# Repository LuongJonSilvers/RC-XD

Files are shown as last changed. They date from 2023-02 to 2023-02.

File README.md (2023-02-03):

# RC-XD
Capstone Project for Embedded Microprocessor System Design Course
Partners: Grant Smith, Sreenivas Krishna Nair, Valente Arroyo, & Akash Chinthamani
This is my capstone project for the final semester at the University Of Wisconsin Madison. This project uses C code with a Hardware abstraction layer(Cypress Cyhal) that is running on a PSoC6. The PSoC6 is a microprocessor that has many features. We were tasked with designing PCB(s), assemblying, coding, debugging, and testing our product. We used Altium Designer and Eclipse IDE for ModusToolbox for this project heavily. The project itself is a APP controlled car platform that can take on many hardware modules to change its funcitonality. This car platform comes with a live camera feed, GPS, crash detection, automatic headlights and a designated app for control. For our final demo we decided to equip the bot with a turret that shot water pellets. Originally this repo was on a partners account which I have transeferred here. The working files that live here include: Presentations/writeup reports, Altium Schematics and PCB docs, C code, python OPENCV code, and Kotlin code files. A project demo can be found following this link : https://www.youtube.com/watch?v=NHO1YES_Jxg&ab_channel=GrantSmith

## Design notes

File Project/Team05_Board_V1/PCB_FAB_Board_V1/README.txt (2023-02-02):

The board outline is defined by a 10mil trace defined on all gerbers.

The board dimensions are 7.2 x 5.8 inches.

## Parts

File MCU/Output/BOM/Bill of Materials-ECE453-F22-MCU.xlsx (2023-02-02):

Description | Designator | Footprint | Quantity | Supplier 1 | Supplier Part Number 1 | Supplier Stock 1
CAP CER 10UF 10V X5R 0805 | C200, C201 | FP-C0805C-DG-MFG | 2 | Digi-Key | 399-C0805C106K8PAC7800CT-ND
CAP CER 0.1UF 50V X7R 0805 | C202, C203 | FP-C0805C-DN-MFG | 2 | Digi-Key | 399-C0805C104K5RAC7800CT-ND
 | C204, C205 | CAPC2013X94X50LL20T25 | 2 | Digi-Key | 478-11894-1-ND
DIODE SCHOTTKY 40V 1A SMA | D200 | FP-SMA-MFG | 1 | Digi-Key | B140-FDICT-ND
SMD mono-color Chip LED, WL-SMCW, Red | LED200 | 0805_A | 1 | Digi-Key | 732-4984-1-ND
SMD mono-color Chip LED, WL-SMCW, Green | LED201 | 0805_A | 1 | Digi-Key | 732-4983-1-ND
RF TXRX MOD BLUETOOTH TRACE ANT | MD200 | FP-CYBLE-416045-02-MFG | 1 | Digi-Key | 428-4622-1-ND
THT Vertical Pin Header WR-PHD, Pitch 2.54 mm, Single Row, 5 pins | P200 | 61300511121 | 1 | Digi-Key | 732-5318-ND
Chip Resistor, 330 Ohm, +/- 1%, 125 mW, -55 to 155 degC, 0805 (2012 Metric), RoHS, Tape and Reel | R200, R202 | RESC2013X60X35LL10T20 | 2 | Digi-Key | 311-330CRCT-ND
Chip Resistor, 10 KOhm, +/- 1%, 0.125 W, -55 to 155 degC, 0805 (2012 Metric), RoHS, Tape and Reel | R201, R203, R204 | RESC2013X60X35NL10T20 | 3 | Digi-Key | 311-10.0KCRCT-ND
Swicth, SPST, 24 V, -35 to 85 degC, 4-Pin SMD, RoHS, Tape and Reel | SW200, SW201 | TECO-FSM4JSMA_V | 2 | Digi-Key | 450-1129-ND
Test Point, 1 Position SMD, RoHS, Tape and Reel | TP200, TP201, TP202, TP203 | KSTN-5019_V | 4 | Digi-Key | 36-5019CT-ND
IC GATE AND 1CH 2-INP SOT23-5 | U200, U201 | FP-DBV0005A-IPC_C | 2 | Digi-Key | 296-SN74AHC1G08DBV3CT-ND
CRYSTAL 32.7680KHZ 6PF SMD | Y200 | FP-ABS07-120-MFG | 1 | Digi-Key | 535-11937-1-ND

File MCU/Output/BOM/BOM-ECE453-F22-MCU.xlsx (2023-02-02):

Description | Designator | Footprint | Quantity | Supplier Part Number 1 | On Hand
CAP CER 10UF 10V X5R 0805 | C200, C300, C302 | CAP_0805 | 3 | 1276-2402-1-ND | y
Cap Aluminum 100uF 10V 20% (6.3 X 5.4mm) SMD 71mA 1000 hr 105°C T/R | C301 | CAP_EEEHA1A101WP | 1 | PCE4169CT-ND | y
CAP CER 10UF 16V X7R 0805 | C400, C401 | CAP_0805 | 2 | 1276-2402-1-ND | y
CAP CER 0.1UF 16V 10% X7R 0805 | C402, C403 | CAP_0805 | 2 | 399-1167-1-ND | y
0805 7 pF 50 V ±0.25 pF Tolerance C0G/NP0 SMT Multilayer Ceramic Capacitor | C404, C405 | CAP_0805 | 2 | 478-10543-6-ND | y
LED GREEN CLEAR THIN 0805 SMD | D200, D300, D401 | LED_GRN_0805 | 3 | 160-1426-1-ND | y
LED SUPER RED CLR THIN 0805 SMD | D400 | LED_RED_0805 | 1 | 160-1427-1-ND | y
CONN SWITCH TACTILE SPST-NO 0.05A 24V | J400, J401 | TE_CONNCECTIVITY_1977223-6_0 | 2 | 450-2054-1-ND | y
Header, 5-Pin | J402, J700, J701, J702, J703, J800, J801, J802, J803, J900, J901, J902, J903, J1000, J1001, J1002, J1003 | HDR1X5 | 17 | S1032EC-05-ND | y
Conn Header Vert 6POS 2.54MM | J804 | HDR1X6 | 1 | S1212E-06-ND
Bluetooth v5.0 Transceiver Module 2.4GHz ~ 2.5GHz Integrated, Trace Surface Mount | MD400 | Cypress_Semiconductor_0_MFG | 1 | 428-4622-1-ND | Y
RES 330 OHM 1% 1/8W 0805 | R200, R301, R400, R402 | RES_0805 | 4 | RMCF0805FT330RCT-ND | y
RES SMD 10K OHM 1% 1/8W 0805 | R401, R403, R404, R800, R801, R900, R901, R1000, R1001 | RES_0805 | 9 | 311-10.0KCRCT-ND | y
RES 0, , 1%, 0.125W, 1/8W 0805 | R802, R803 | RES_0805 | 2 | P0.0ACT-ND | y
Test Point SMD 1206 | TP200, TP201, TP202, TP300, TP400, TP401, TP402 | TP-SMC-1206 | 7 | A106143CT-ND | y
Supervisory Circuits Volt Sup Det 2.3-6V | U200 | ROHM-SSOP3_ROM-M | 1 | BD49K45G-TLCT-ND | y
LDO Regulator Pos 3.3V 0.1A 3-Pin TO-92 Bulk / IC REG LDO 3.3V 0.1A TO92-3 | U300 | TO92127P520H660-3 | 1 | LP2950CZ-3.3/NOPB-ND | y
Processor Supervisor 3.2V 1 Active Low/CMOS 3-Pin SSOP T/R | U301 | ROHM-SSOP3_ROM-M | 1 | BD49K32G-TLCT-ND | y
TLV1117LV 1-A, Positive Fixed Vo | U302 | SOT230P700X180-4N | 1 | 296-35976-1-ND | Y
Rectifier Diode Schottky 40V 1A 2-Pin SMA T/R | U400, U800 | CDBA-HF | 2 | 641-1762-1-ND | y
AND Gate 1-Element 2-IN CMOS 5-Pin SOT-23 T/R | U401, U402 | SOT23-5-AND | 2 | 296-SN74AUP1G08DBVRCT-ND | y
Crystal 0.032768MHz ±20ppm (Tol) 7pF Flexural 70000Ohm 2-Pin Ultra Mini-CSMD T/R | Y400 | XTAL_ECS-.327-7-34B-TR | 1 | XC1656CT-ND | y

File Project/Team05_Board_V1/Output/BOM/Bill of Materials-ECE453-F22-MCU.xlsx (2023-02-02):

Description | Designator | Footprint | LibRef | Quantity | Manufacturer | Manufacturer Part Number | Supplier 1 | Supplier Part Number 1
BATTERY LITHIUM 3V COIN 20MM | BT1 | FP-BR-2032-HEN-MFG | CMP-05417-000004-1 | 1 | Panasonic | BR-2032/HEN | Digi-Key | P196-ND
BATT HOLDER 18650 3 CELL PC PIN | BT2 | FP-BK-18650-PC6-MFG | CMP-136234-000001-1 | 1 | MPD (Memory Protection Devices) | BK-18650-PC6 | Digi-Key | BK-18650-PC6-ND
CAP CER 1PF 50V C0G/NPO 0805 | C1, C3, C7 | FP-CC0805-0_1-0_7-IPC_B | CMP-03422-001522-1 | 3 | Yageo | CC0805BRNPO9BN1R0 | Digi-Key | 311-4124-1-ND, 311-4124-6-ND
CAP CER 1UF 10V X7R 0805 | C2, C4, C8 | FP-CC0805-0_85-MFG | CMP-03422-000182-1 | 3 | Yageo | CC0805KKX7R6BB105 | Digi-Key | 311-1458-1-ND, 311-1458-2-ND
CAP CER 0.1UF 100V X7R 0805 | C5, C6 | FP-C0805C-DN-MFG | CMP-2007-03648-2 | 2 | KEMET | C0805C104K1RACAUTO | Digi-Key | 399-6926-1-ND
10 uF Capacitor | C9 | CAPC2014X150X70LL20 | CMP-2007-00024-1 | 1 | AVX Interconnect / Elco | TACR106M006RTA | Digi-Key | 478-5225-1-ND
Multilayer Ceramic Capacitors 100nF ±10% 50V X8R SMD 0805 (0.1 uF) | C10 | FP-C2012-125-0_2-MFG | CMP-08246-005122-1 | 1 | TDK | C2012X8R1H104K125AA | Digi-Key | 445-2514-6-ND
CAP CER 10UF 10V X5R 0805 | C200, C201 | FP-C0805C-DG-MFG | CMP-2007-03243-2 | 2 | Kemet | C0805C106K8PACTU | Digi-Key | 399-C0805C106K8PAC7800CT-ND
CAP CER 0.1UF 50V X7R 0805 | C202, C203 | FP-C0805C-DN-MFG | CMP-2007-00279-2 | 2 | KEMET | C0805C104K5RACTU | Digi-Key | 399-C0805C104K5RAC7800CT-ND
CAP CER 6PF 50V | C204, C205 | CAPC2013X94X50LL20T25 | CMP-2007-04344-1 | 2 | AVX Interconnect / Elco |  | Digi-Key | 478-11894-1-ND
LED GREEN CLEAR SMD | D1 | FP-LTST-C171KGKT-MFG | CMP-22017-000037-1 | 1 | Vishay Lite-On | LTST-C171KGKT | Digi-Key | 160-1426-1-ND
DIODE SCHOTTKY 40V 1A SMA | D2, D200 | FP-SMA-MFG | CMP-2000-05096-2 | 2 | Diodes, [NoParam] | B140-13-F, [NoParam] | Digi-Key | B140-FDICT-ND
Signal Line Ferrite Bead 300Ω @ 100MHz 300mA DCR 700mΩ SMD 0603 | FB1 | FP-MMZ1608-0_8-MFG | CMP-08257-000452-1 | 1 | TDK | MMZ1608D301BTA00 | TTI | MMZ1608D301BTA00
RP-SMA Female Right Angle PCB Mount Connector, Thru-Hole | J1 | CON-REVSMA-RA | CMP-0168-00005-1 | 1 | Linx | CONREVSMA002 | Digi-Key | CONREVSMA002-ND
SMD mono-color Chip LED, WL-SMCW, Red | LED1, LED2, LED200 | 0805_A | CMP-1426-00011-1 | 3 | Wuerth Elektronik | 150080RS75000, [NoParam] | Digi-Key | 732-4984-1-ND
SMD mono-color Chip LED, WL-SMCW, Green | LED201 | 0805_A | CMP-1426-00007-1 | 1 | Wuerth Elektronik |  | Digi-Key | 732-4983-1-ND
RF TXRX MOD BLUETOOTH TRACE ANT | MD200 | FP-CYBLE-416045-02-MFG | CMP-12964-000002-1 | 1 | Cypress Semiconductor | CYBLE-416045-02 | Digi-Key | 428-4622-1-ND
THT Vertical Pin Header WR-PHD, Pitch 2.54 mm, Single Row, 5 pins | P200 | 61300511121 | CMP-1502-01068-1 | 1 | Wurth Elektronik |  | Digi-Key | 732-5318-ND
MOSFET N-CH 60V 260MA SOT-23 | Q1 | FP-318-08-IPC_A | CMP-1058-00769-2 | 1 | ON Semiconductor | 2N7002ET1G | Digi-Key | 2N7002ET1GOSCT-ND
SMD Chip Resistor, Thin Film, 100Ω, 100 V, 0805 [2012 Metric], 100 mW, 0.1%, RN73 Series | R1 | FP-RN732A-MFG | CMP-03211-001241-1 | 1 | TE Connectivity | RN73C2A100RBTG
Chip Resistor, 10 KOhm, +/- 1%, 0.125 W, -55 to 155 degC, 0805 (2012 Metric), RoHS, Tape and Reel | R2, R4, R201, R203, R204 | RESC2013X60X35NL10T20 | CMP-1659-00013-4 | 5 | Yageo | RC0805FR-0710KL, [NoParam] | Digi-Key | 311-10.0KCRCT-ND
Chip Resistor, 330 Ohm, +/- 1%, 125 mW, -55 to 155 degC, 0805 (2012 Metric), RoHS, Tape and Reel | R3, R200, R202 | RESC2013X60X35LL10T20 | CMP-2000-06960-1 | 3 | Yageo | RC0805FR-07330RL, [NoParam] | Digi-Key | 311-330CRCT-ND
511 Ohm Resisitor | R5 | RESC2013X70X40ML20T20 | CMP-2001-00217-1 | 1 | Panasonic | ERJ-6ENF5110V | Digi-Key | P511CCT-ND
2.7kΩ ±5% 0.125W 0805 Thick Film Chip Resistor AEC-Q200 compliant | R6, R7 | FP-RMCF0805-MFG | CMP-26527-006669-1 | 2 | Stackpole Electronics | RMCF0805JT2K70 | Digi-Key | RMCF0805JT2K70CT-ND
TACT 4.5 X 4.5, 3.8 MM H, 2.5N, | SW1 | FP-PTS647SK38SMTR2LFS-MFG | CMP-10040-000033-1 | 1 | ITT C&K | PTS647SK38SMTR2LFS | Digi-Key | PTS647SK38SMTR2LFSCT-ND
Swicth, SPST, 24 V, -35 to 85 degC, 4-Pin SMD, RoHS, Tape and Reel | SW2, SW3, SW200, SW201 | TECO-FSM4JSMA_V | CMP-2000-05602-2 | 4 | TE Connectivity | FSM4JSMA, [NoParam] | Digi-Key | 450-1129-ND
Test Point, 1 Position SMD, RoHS, Tape and Reel | TP_AFTER_REG_3V3, TP_AFTER_REG_5V0, TP_AFTER_SUPRVSR_3V3, TP_AFTER_SUPRVSR_5V0, TP_BEFORE_REG, TP_CS_ACCEL1, TP_GND_ACCEL1, TP_GND_GPS1, TP_GND_LIGHT1, TP_GND_MCU1, TP_GND_MCU2, TP_GND_MCU3, TP_GND_POWER, TP_GPS_ANTENNA1, TP_GPS_LCKIND1, TP_GPS_RST1, TP_GPS_RX1, TP_GPS_TX1, TP_GPS_VCC1, TP_GPS_VOUT1, TP_INT1, TP_INT2, TP_INT_LIGHT1, TP_MAN_RST_3V3, TP_MAN_RST_5V0, TP_MCU_RST, TP_SCL_ACCEL1, TP_SCL_LIGHT1, TP_SDA_ACCEL1, TP_SDA_LIGHT1 | KSTN-5019_V | CMP-1672-00008-1 | 30 | Keystone Electronics, [NoParam] | 5019, [NoParam] | Digi-Key, Newark | 36-5019CT-ND, 06W4636
RM Series GPS Receiver Module - Tape & Reel | U1 | RXM-GPS-RM-T_LNX | GPS | 1 | Linx | RXM-GPS-RM-T | Digi-Key | RXM-GPS-RM-TCT-ND
IC REG LINEAR 3.3V/5V SOT23-6 | U2 | FP-SOT23-6LD-PL-1-MFG | CMP-06324-000039-1 | 1 | Microchip | MIC5211-LXYM6-TR | Digi-Key | 576-2749-1-ND
IC SUPERVISOR 3.08V SOT143-4 | U3 | SOT143 | APX811-31UG-7 | 1 | Diodes | APX811-31UG-7 | Digi-Key | APX811-31UG-7DICT-ND
4-Pin Microprocessor Supervisor With Manual Reset, 5.5V, 20µA, -40°C to 85°C | U4 | SOT143 | APX811-46UG-7 | 1 | Diodes | APX811-46UG-7 | Digi-Key | APX811-46UG-7DICT-ND
Light-to-Digital Converter with I2C Interface, 2.7 to 3.6 V, -30 to 70 degC, FN-6, Pb-Free, Reel | U5 | AMS-FN-6-2400X2000DE_V | CMP-0865-00001-1 | 1 | AMS | TSL25911FN | Avnet | 300150004
ACCELEROMETER 2-8G I2C/SPI 24QFN | U6 | FP-IIS328DQTR-MFG | CMP-12175-000005-1 | 1 | STMicroelectronics | IIS328DQTR | Newark | 83Y4299
IC GATE AND 1CH 2-INP SOT23-5 | U200, U201 | FP-DBV0005A-IPC_C | CMP-04903-000082-1 | 2 |  |  | Digi-Key | 296-SN74AHC1G08DBV3CT-ND
CRYSTAL 32.7680KHZ 6PF SMD | Y200 | FP-ABS07-120-MFG | CMP-2000-07587-2 | 1 |  |  | Digi-Key | 535-11937-1-ND

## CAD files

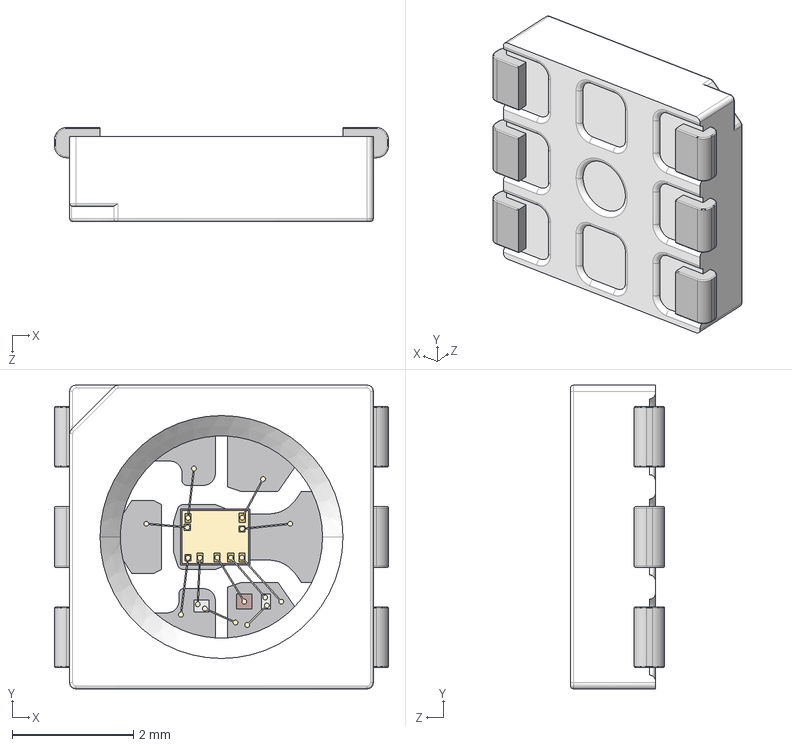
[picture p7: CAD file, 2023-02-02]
Custom/3D/APA102C.STEP
5.50 x 5.00 x 1.55 mm

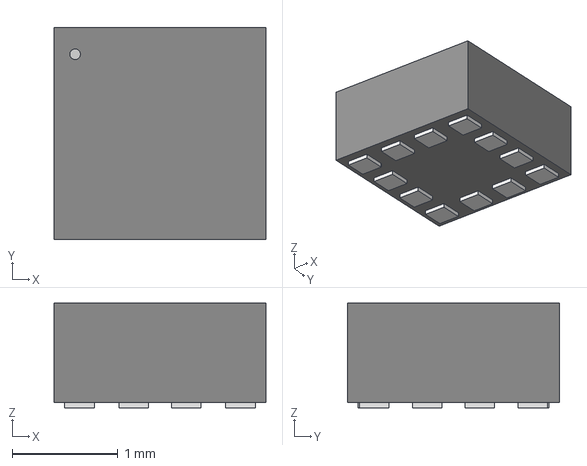
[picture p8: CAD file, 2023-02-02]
Lab_3_Serial_Interface_Board_Build/AltiumDesigner/2022-09-29_20-19-19/MXC6655XA_MEM.step
2.01 x 2.01 x 0.993 mm

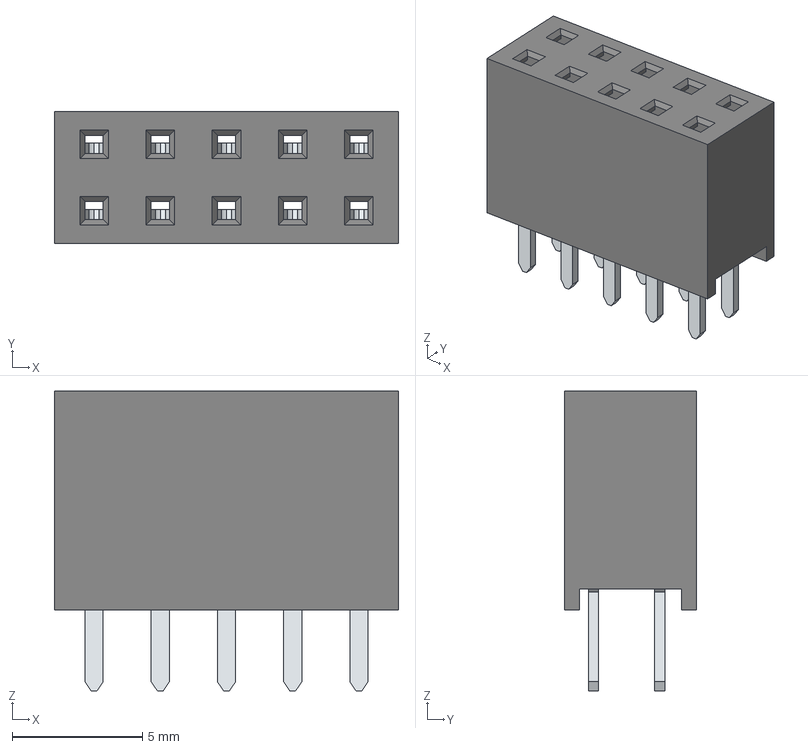
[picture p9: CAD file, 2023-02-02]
Project/Team05_Board_V1/3D/STEP-61301021821-rev1.stp
13.2 x 5.08 x 11.5 mm
6130xx21821_PIN x 10

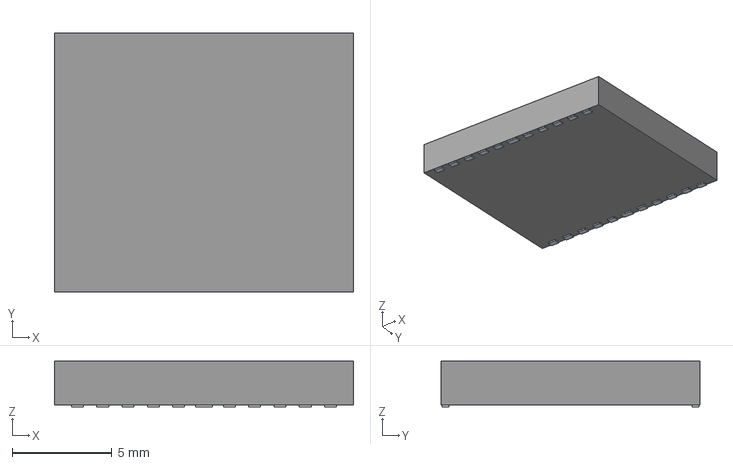
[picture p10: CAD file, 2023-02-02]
Project/Team05_Board_V1/RXM-GPS-RM-T/3D/RXM-GPS-RM-T.stp
15.0 x 13.0 x 2.30 mm
Pins

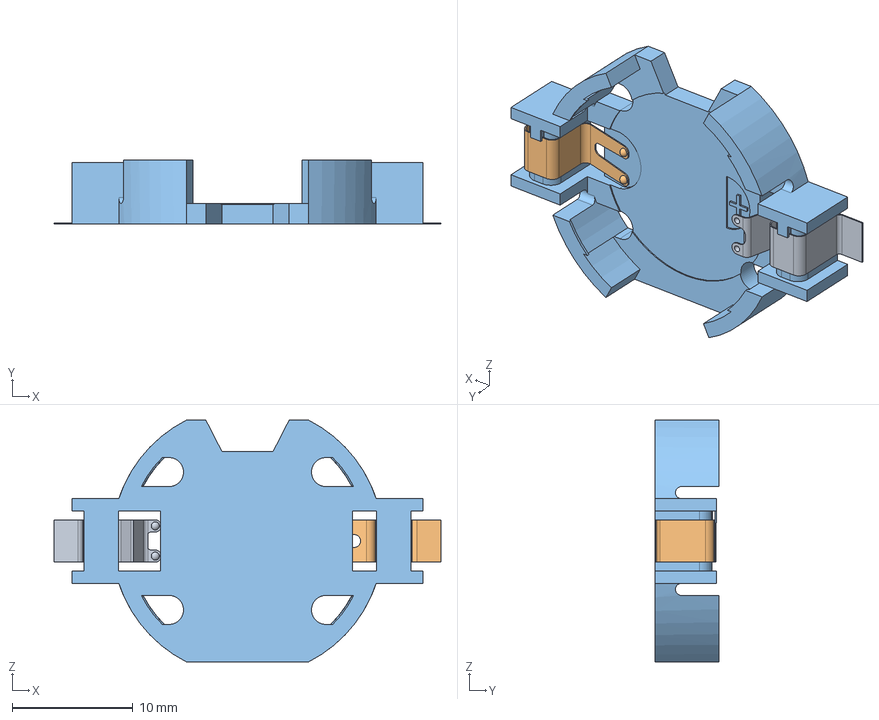
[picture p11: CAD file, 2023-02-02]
Custom/3D/BU2032SM-HD-GCR2032 Battery Holder.stp
32.0 x 5.30 x 20.0 mm

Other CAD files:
Project/Team05_Board_V1/RXM-GPS-RM-T/Allegro/rxmgpsrmt.psm
Project/Team05_Board_V1/RXM-GPS-RM-T/DEHDL/rxm_gps_rm_t/chips/chips.prt

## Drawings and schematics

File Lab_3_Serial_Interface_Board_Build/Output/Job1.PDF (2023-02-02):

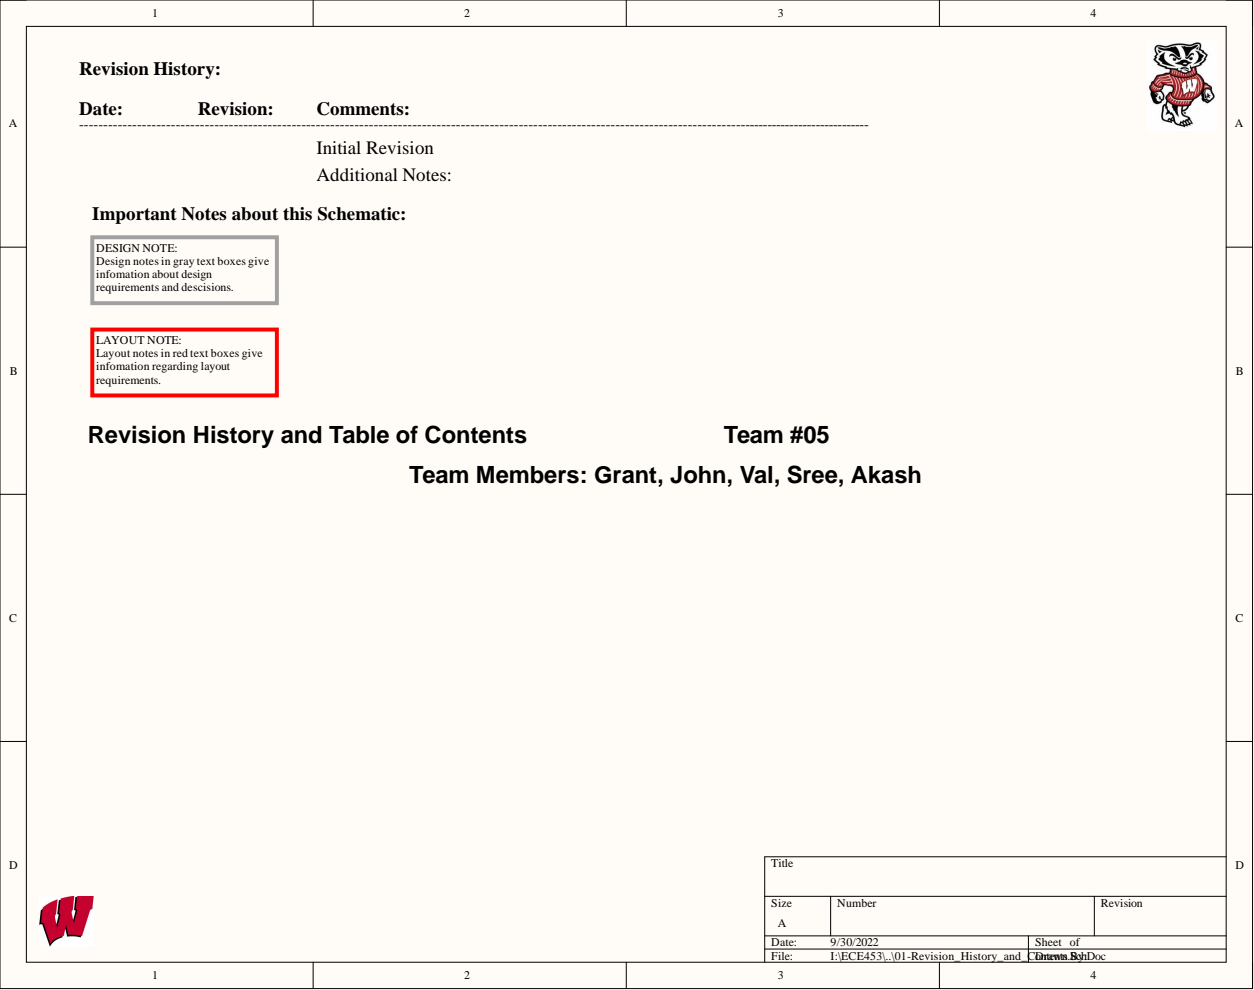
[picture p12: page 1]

Important Notes about this Schematic:

DESIGN NOTE:
Design notes in gray text boxes give
infomation about design
requirements and descisions.

LAYOUT NOTE:
Layout notes in red text boxes give
infomation regarding layout
requirements.

Revision History and Table of Contents

Team Members: Grant, John, Val, Sree, Akash

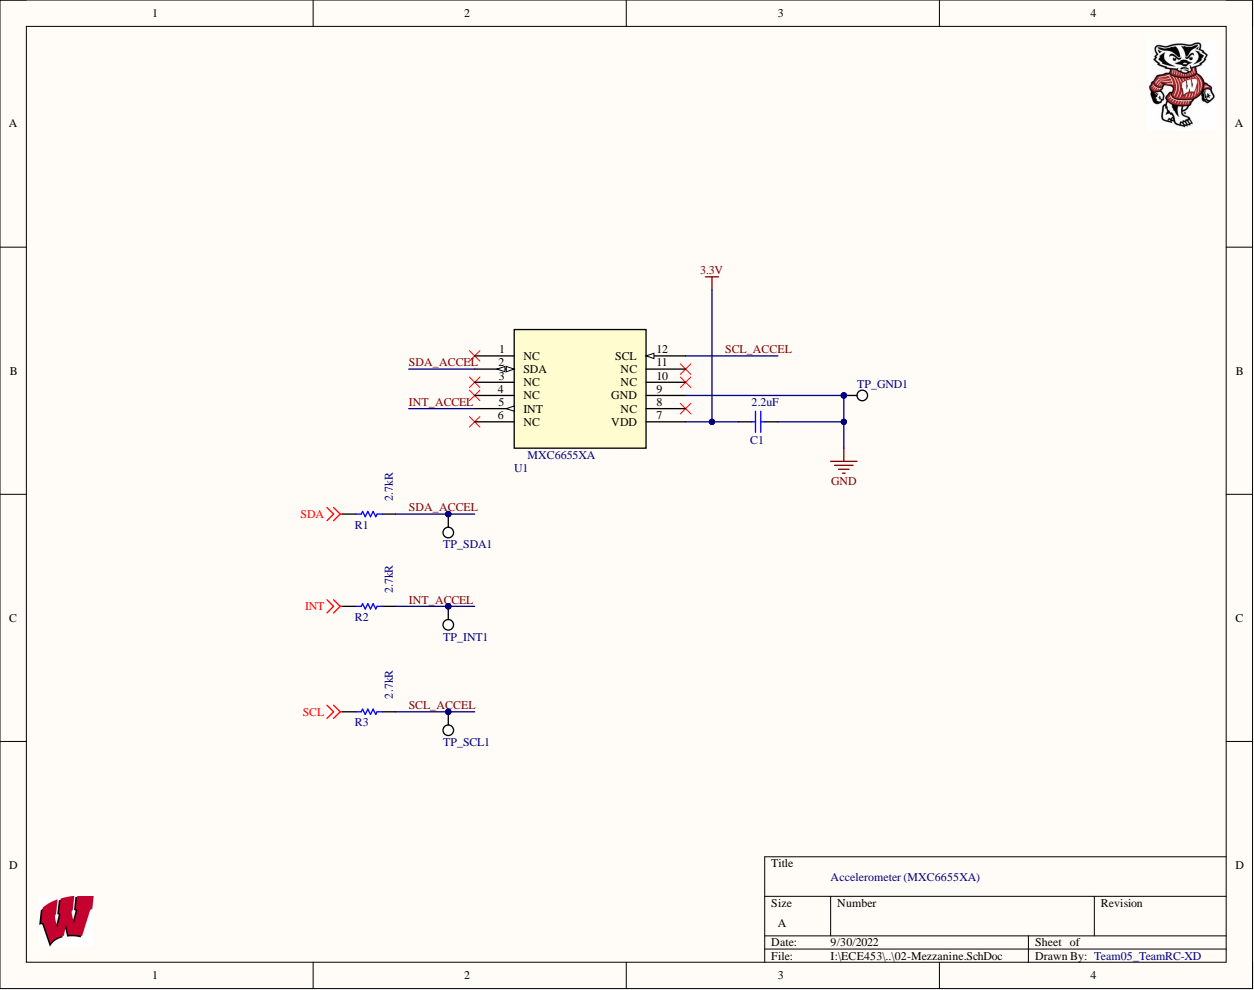
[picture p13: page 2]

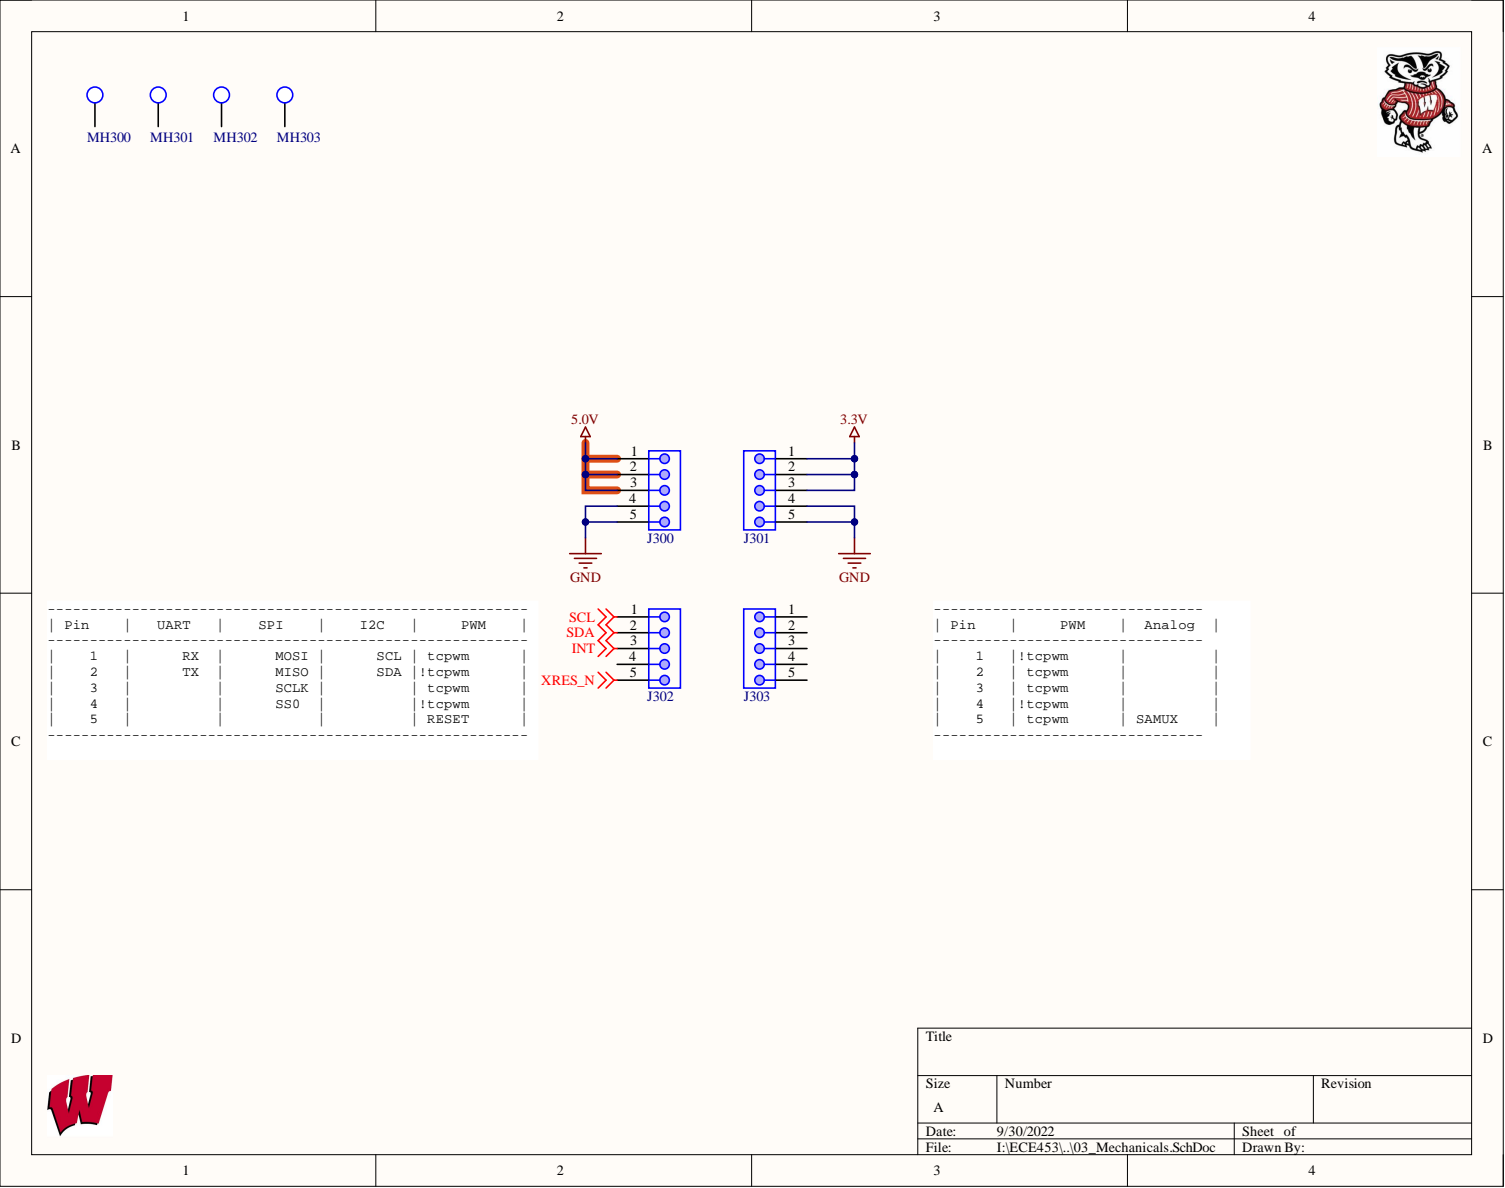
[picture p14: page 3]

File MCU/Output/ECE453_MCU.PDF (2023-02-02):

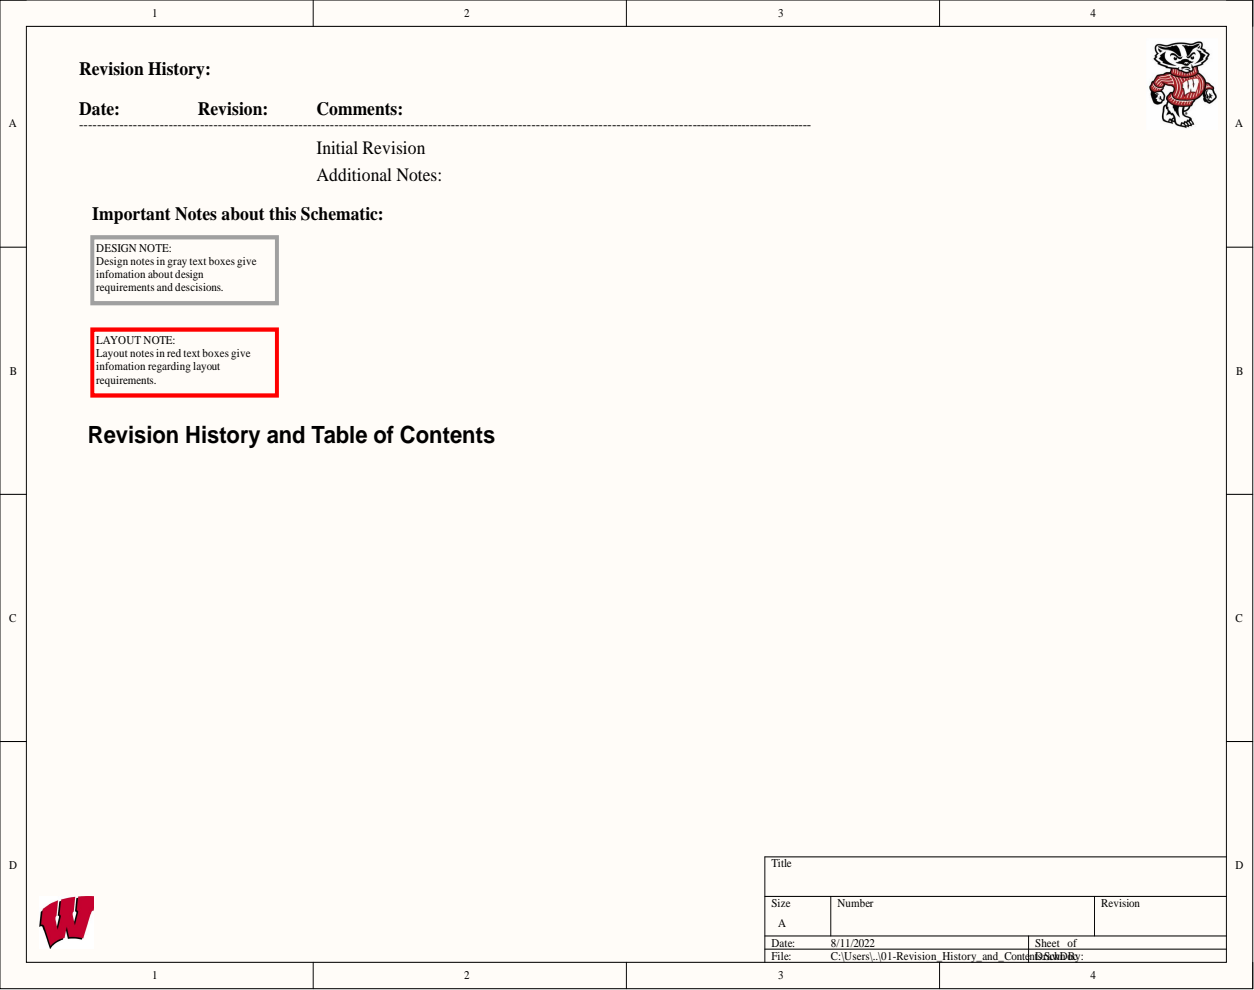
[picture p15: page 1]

Important Notes about this Schematic:

DESIGN NOTE:
Design notes in gray text boxes give
infomation about design
requirements and descisions.

LAYOUT NOTE:
Layout notes in red text boxes give
infomation regarding layout
requirements.

Revision History and Table of Contents

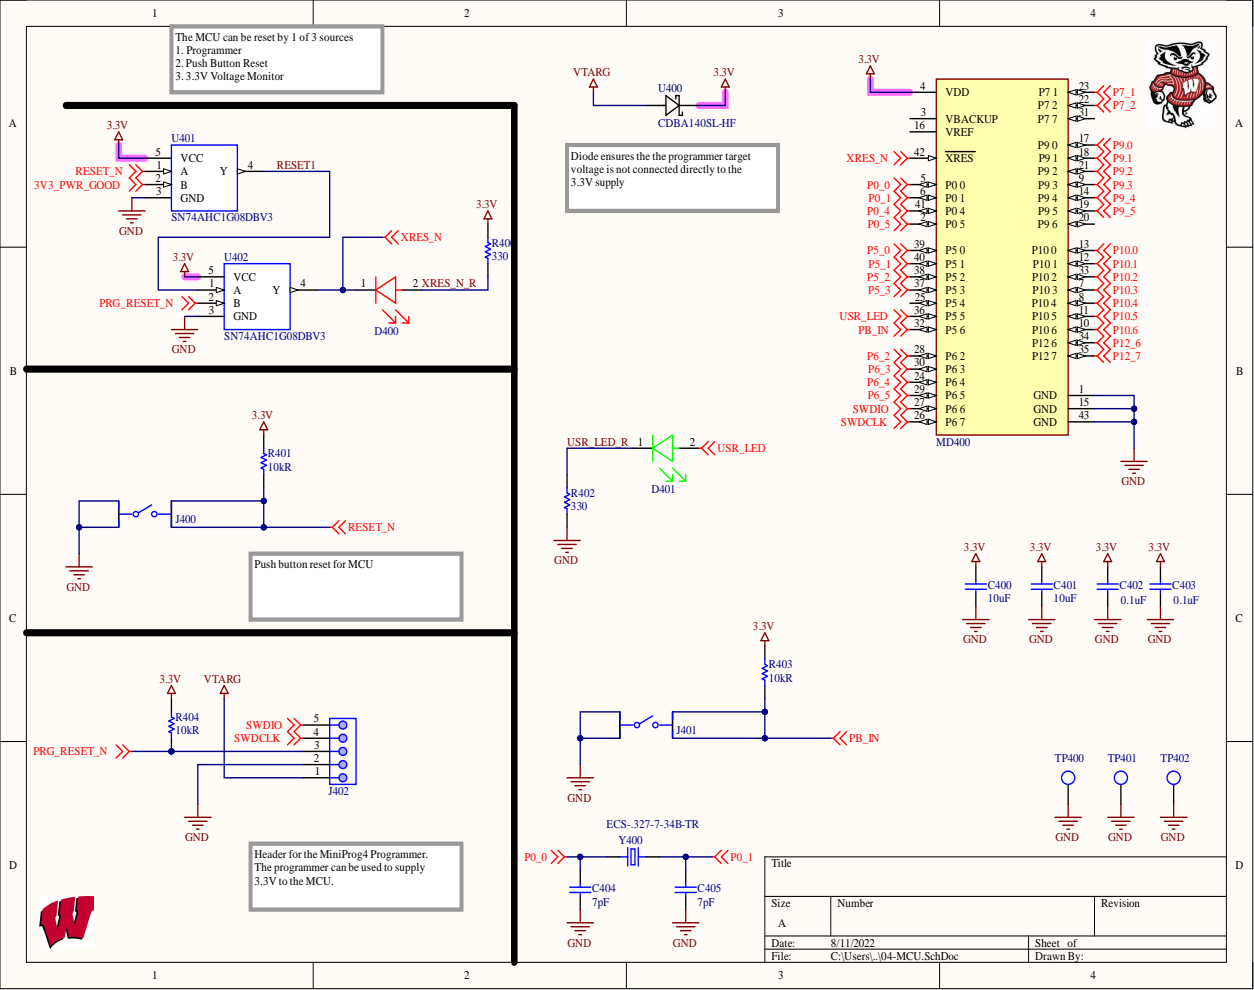
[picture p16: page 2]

The MCU can be reset by 1 of 3 sources
1. Programmer
2. Push Button Reset
3. 3.3V Voltage Monitor

Diode ensuresthe the programmer target
voltage is not connected directly to the
3.3V supply

Push button reset for MCU

Header for the MiniProg4 Programmer.
The programmer can be used to supply
3.3V to the MCU.

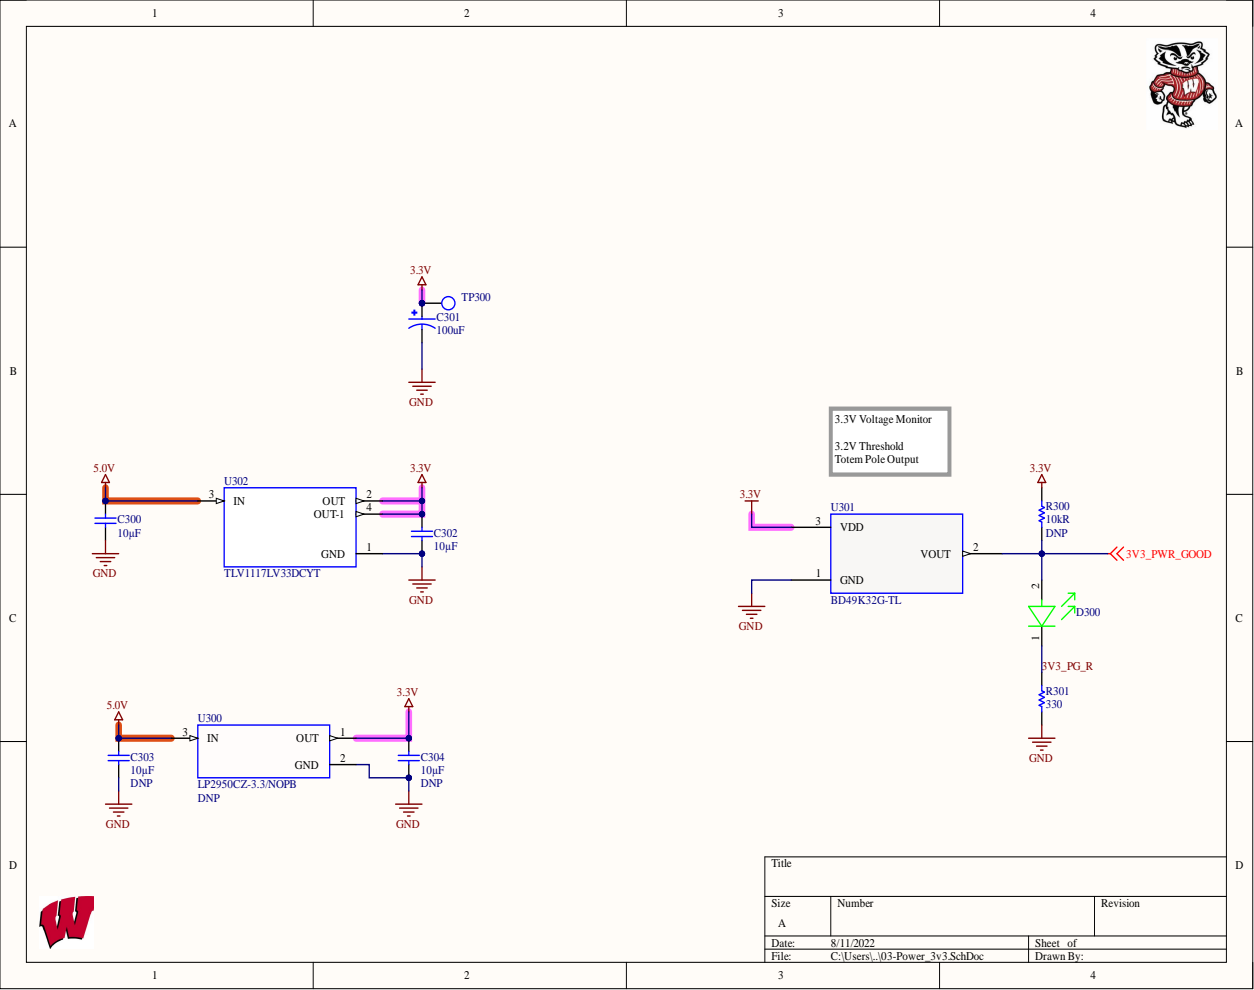
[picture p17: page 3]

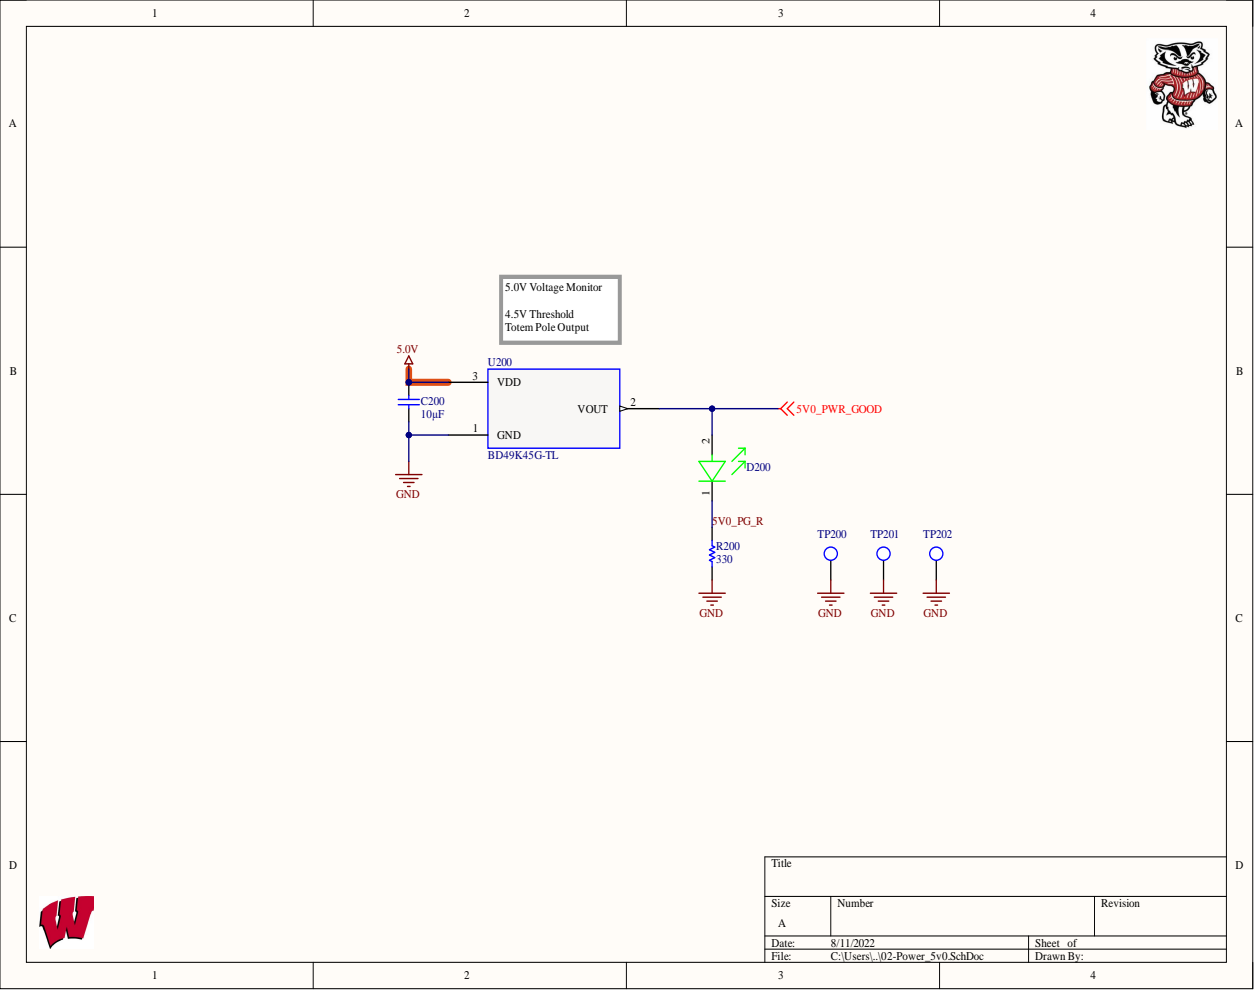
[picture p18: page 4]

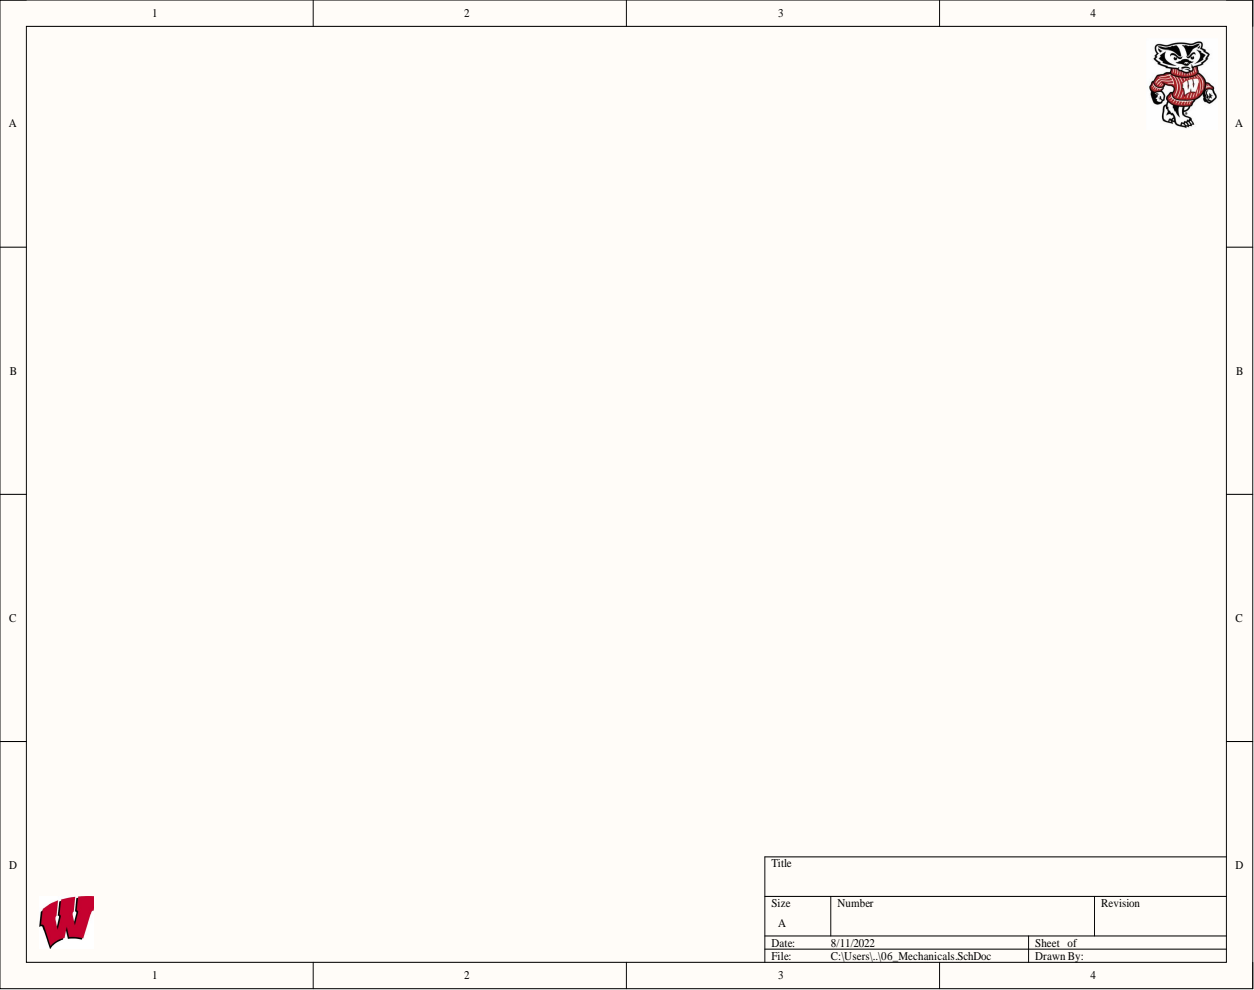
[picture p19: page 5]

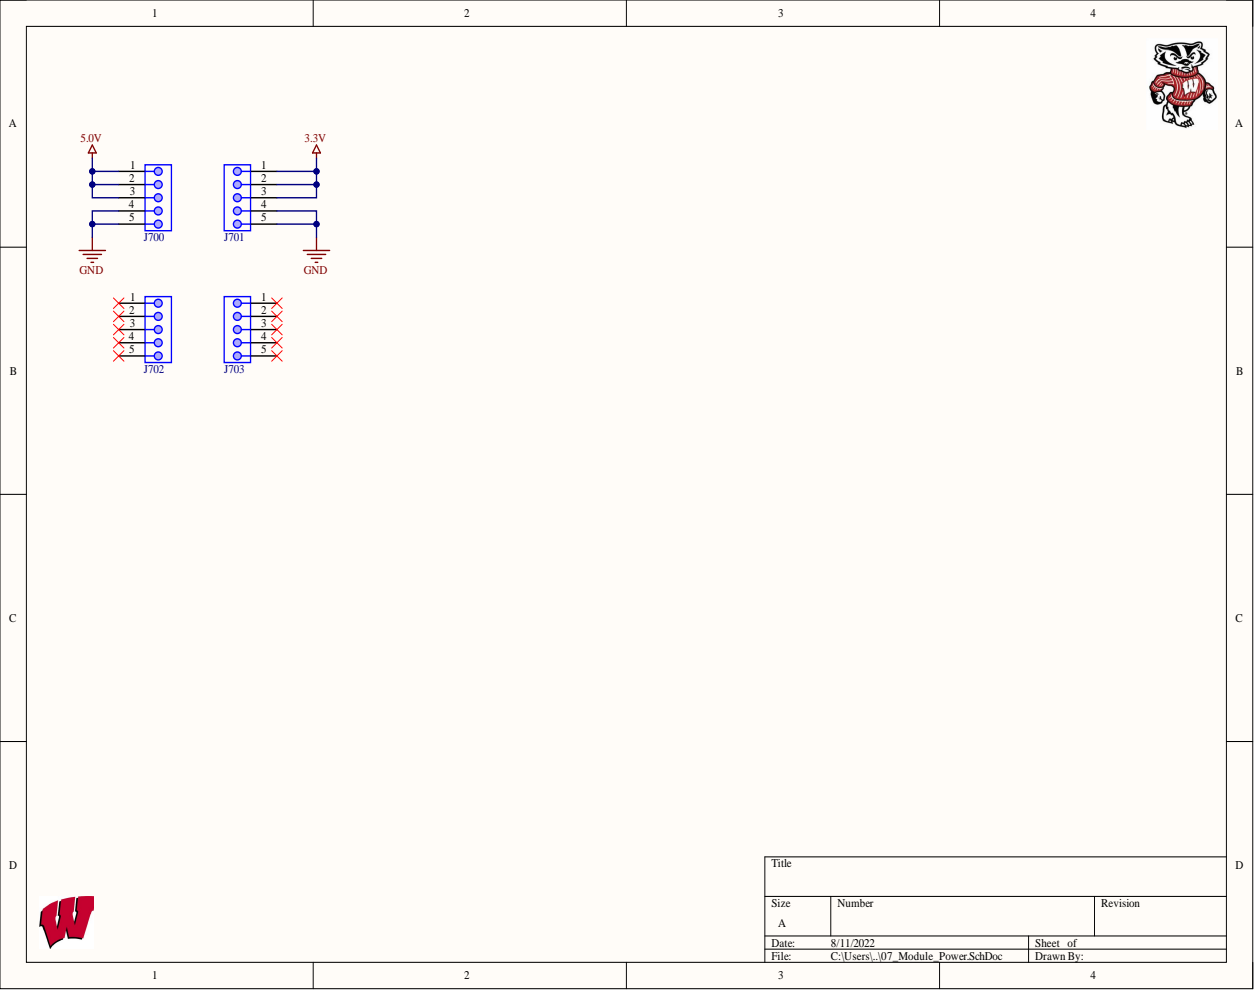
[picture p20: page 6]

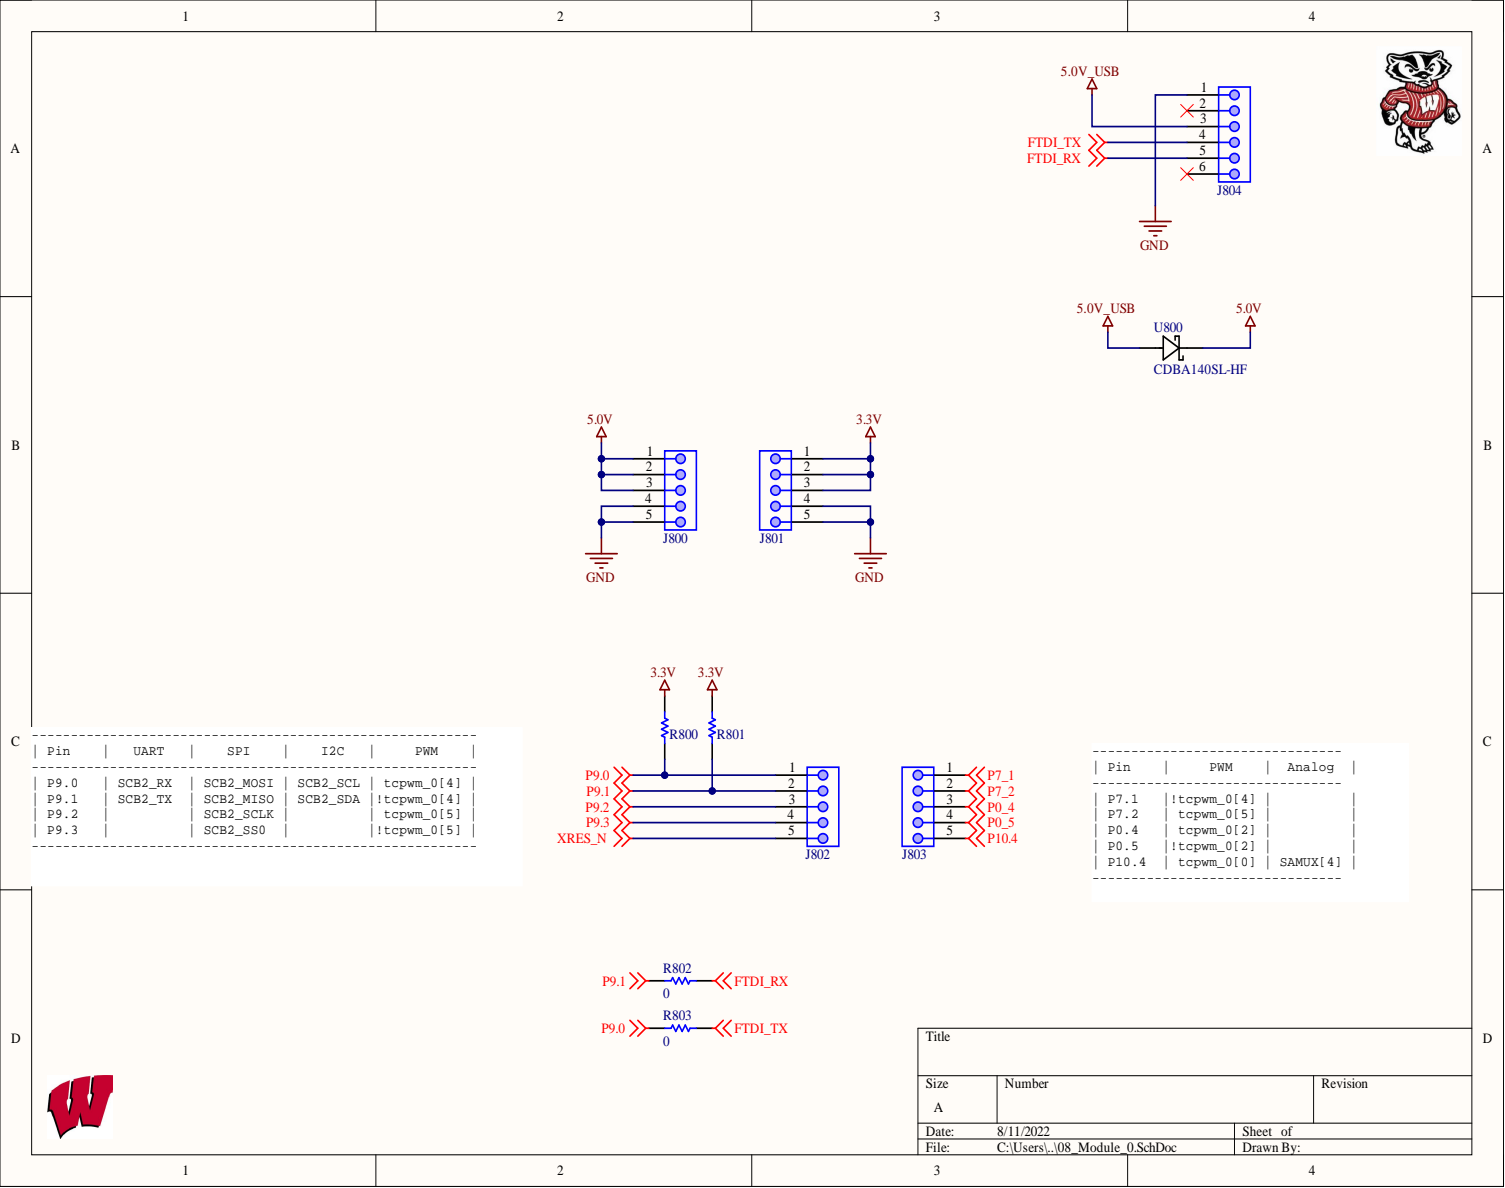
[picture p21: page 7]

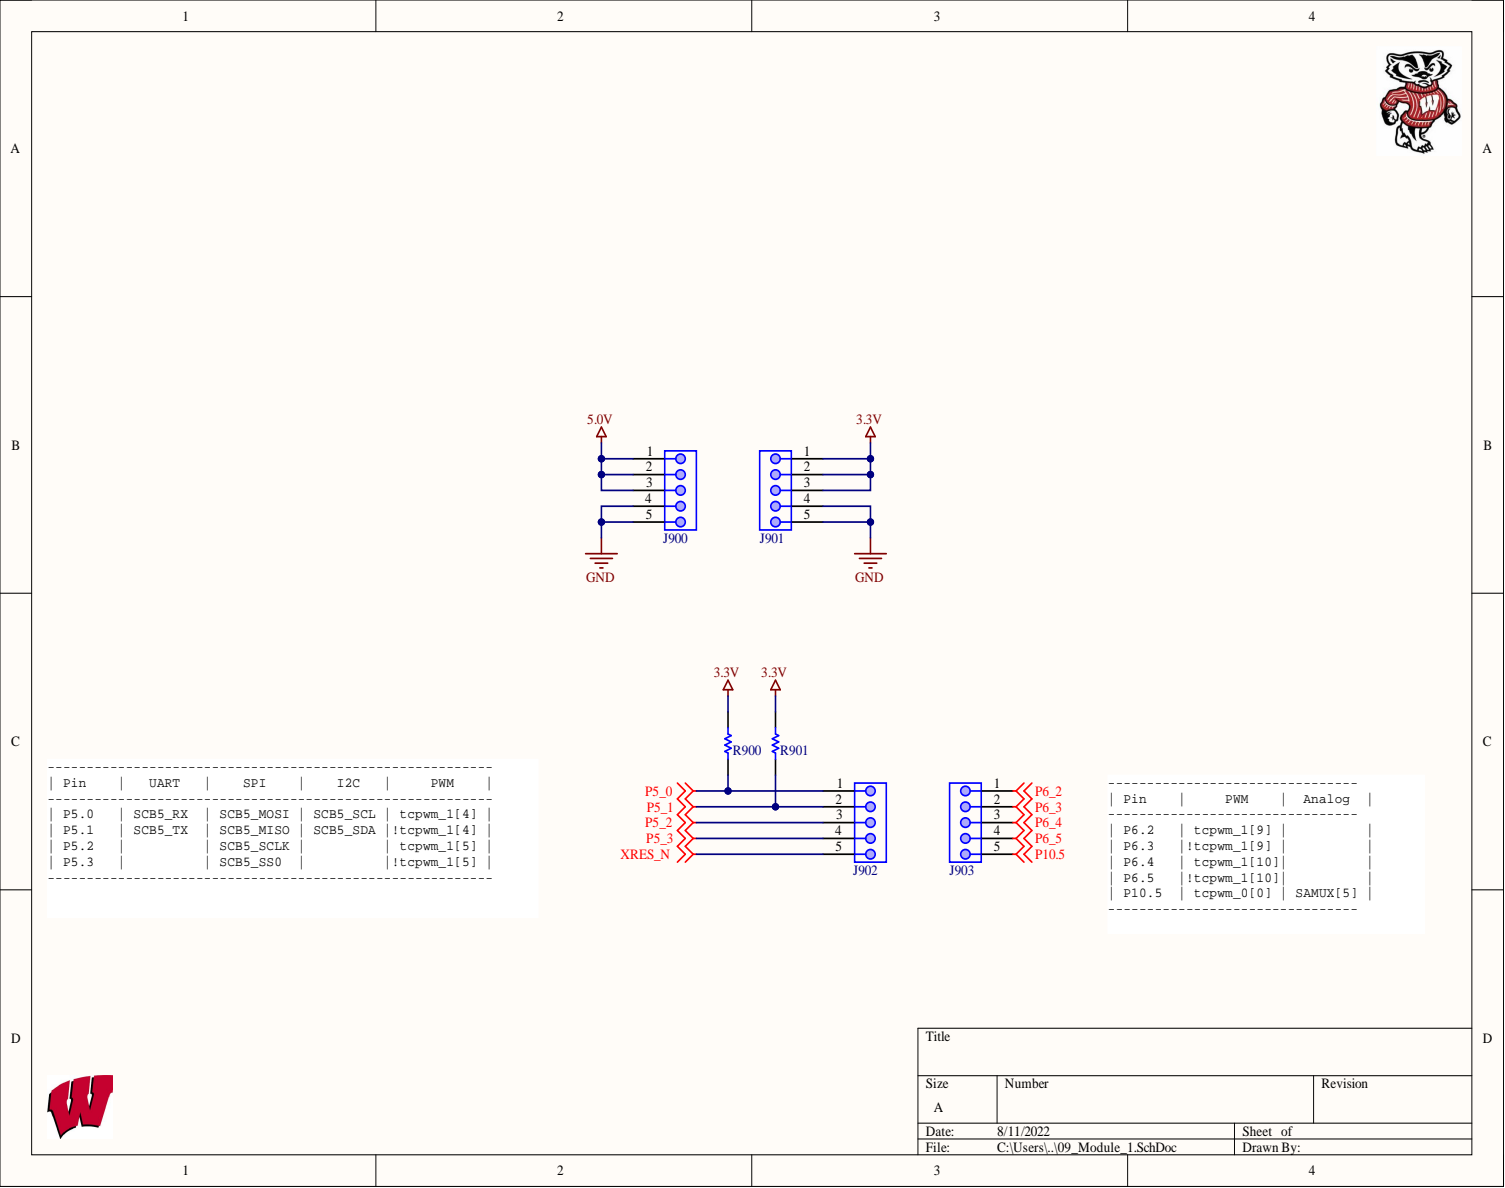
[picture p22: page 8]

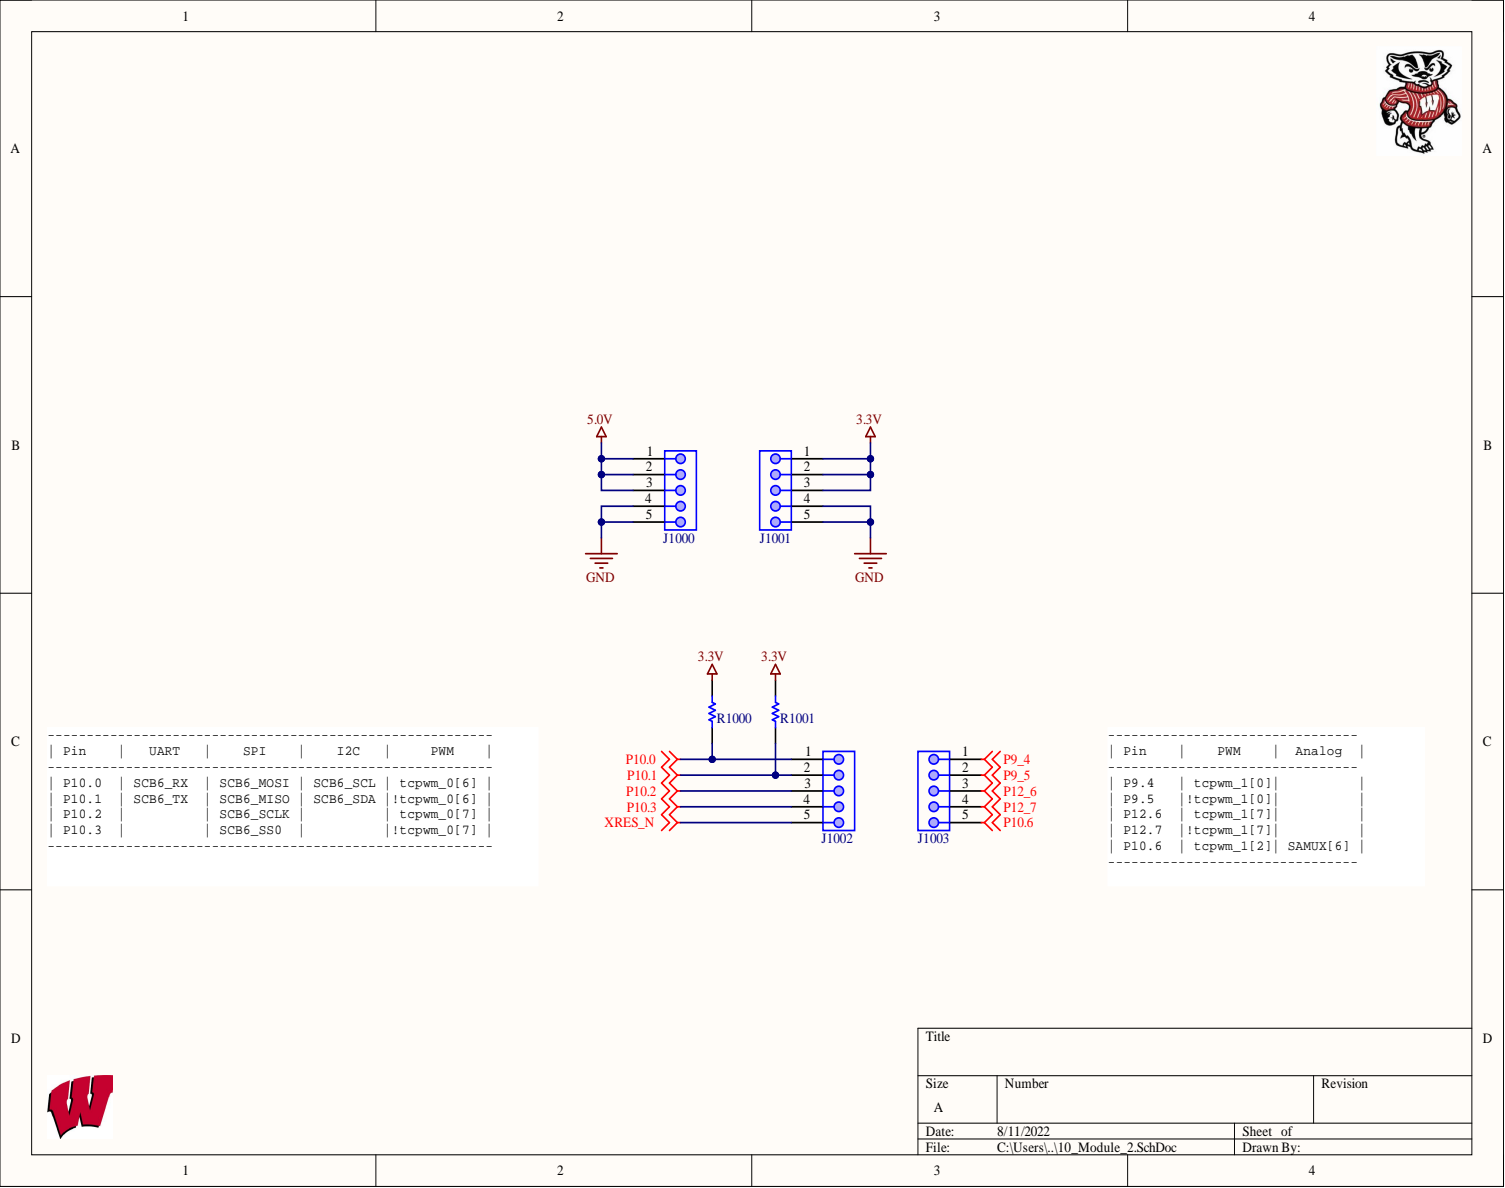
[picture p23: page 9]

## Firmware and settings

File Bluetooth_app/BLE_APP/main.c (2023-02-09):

/******************************************************************************
 * File Name: main.c
 *
 * Description: This is source code for the PSoC 6 MCU with BLE Find Me code
 *              example.
 *
 * Related Document: README.md
 *
 *******************************************************************************
 * Copyright 2019-2021, Cypress Semiconductor Corporation (an Infineon company) or
 * an affiliate of Cypress Semiconductor Corporation.  All rights reserved.
 *
 * This software, including source code, documentation and related
 * materials ("Software") is owned by Cypress Semiconductor Corporation
 * or one of its affiliates ("Cypress") and is protected by and subject to
 * worldwide patent protection (United States and foreign),
 * United States copyright laws and international treaty provisions.
 * Therefore, you may use this Software only as provided in the license
 * agreement accompanying the software package from which you
 * obtained this Software ("EULA").
 * If no EULA applies, Cypress hereby grants you a personal, non-exclusive,
 * non-transferable license to copy, modify, and compile the Software
 * source code solely for use in connection with Cypress's
 * integrated circuit products.  Any reproduction, modification, translation,
 * compilation, or representation of this Software except as specified
 * above is prohibited without the express written permission of Cypress.
 *
 * Disclaimer: THIS SOFTWARE IS PROVIDED AS-IS, WITH NO WARRANTY OF ANY KIND,
 * EXPRESS OR IMPLIED, INCLUDING, BUT NOT LIMITED TO, NONINFRINGEMENT, IMPLIED
 * WARRANTIES OF MERCHANTABILITY AND FITNESS FOR A PARTICULAR PURPOSE. Cypress
 * reserves the right to make changes to the Software without notice. Cypress
 * does not assume any liability arising out of the application or use of the
 * Software or any product or circuit described in the Software. Cypress does
 * not authorize its products for use in any products where a malfunction or
 * failure of the Cypress product may reasonably be expected to result in
 * significant property damage, injury or death ("High Risk Product"). By
 * including Cypress's product in a High Risk Product, the manufacturer
 * of such system or application assumes all risk of such use and in doing
 * so agrees to indemnify Cypress against all liability.
 *******************************************************************************/

/******************************************************************************
 * Header files
 ******************************************************************************/
#include "cy_pdl.h"
#include "cy_retarget_io.h"
#include "cybsp.h"
#include "cyhal.h"
#include "ble_findme.h"
#include "main.h"
#include "usr_btn.h"
#include "stdlib.h"
#include "motor_controls.h"
#include "accelerometer.h"
#include "light_sensor2.h"
#include "timer.h"
#include "console.h"
#include "uart.h"
#include <stdio.h>
#include <string.h>
#include <assert.h>
#include <ctype.h>

#define PERIPHERAL_LOG_ON true

volatile int send_crash_ble = 0;

/* drive train & servo*/
volatile int ble_duty_cycle_drive_train;
volatile int ble_duty_cycle_servo;
cyhal_pwm_t pwm_obj_drive_train;
cyhal_pwm_t pwm_obj_servo;
/*GPS unit*/
extern uint8_t rx_buf[RX_BUF_SIZE];
volatile uint8_t GPS_BUFFER[200];
extern cyhal_uart_t uart_obj;

volatile int turret_fire = 0;
volatile char *gps_latitude;
volatile char *gps_longitude;
volatile int gps_N_1_S_0;
volatile int gps_E_1_W_0;

void turret_fire_ble(void)
{
    turret_fire ? cyhal_gpio_write(TURRET_PIN, true) : cyhal_gpio_write(TURRET_PIN, false);
    return;
}

int gps_split(char *str, char c, char ***arr)
{
    int count = 1;
    int token_len = 1;
    int i = 0;
    char *p;
    char *t;

    p = str;
    while (*p != '\0')
    {
        if (*p == c)
            count++;
        p++;
    }

    *arr = (char **)malloc(sizeof(char *) * count);
    if (*arr == NULL)
        exit(1);

    p = str;
    while (*p != '\0')
    {
        if (*p == c)
        {
            (*arr)[i] = (char *)malloc(sizeof(char) * token_len);
            if ((*arr)[i] == NULL)
                exit(1);

            token_len = 0;
            i++;
        }
        p++;
        token_len++;
    }
    (*arr)[i] = (char *)malloc(sizeof(char) * token_len);
    if ((*arr)[i] == NULL)
        exit(1);

    i = 0;
    p = str;
    t = ((*arr)[i]);
    while (*p != '\0')
    {
        if (*p != c && *p != '\0')
        {
            *t = *p;
            t++;
        }
        else
        {
            *t = '\0';
            i++;
            t = ((*arr)[i]);
        }
        p++;
    }

    return count;
}

void global_timer_peripherals(void)
{
    float lumen;
    if (global_timer_interrupt_flag)
    {
        lumen = OPT3001_read_light();

        (lumen < 7500) ? cyhal_gpio_write(P12_7, true) : cyhal_gpio_write(P12_7, false);

        if (crash_occured())
        {
            send_crash_ble = 1;
        }
        global_timer_interrupt_flag = false;

        if (PERIPHERAL_LOG_ON)
        {
            printf("********LUMEN : %f********** \r\n\n", lumen);
            printf("CRASH_VAL :: %f\r\n", (float)(accelerometer_x_axis() * accelerometer_x_axis() + accelerometer_y_axis() * accelerometer_y_axis() + accelerometer_z_axis() * accelerometer_z_axis()));
            printf("X_AXIS :: %d, Y_AXIS :: %d, Z_AXIS :: %d\r\n", accelerometer_x_axis(), accelerometer_y_axis(), accelerometer_z_axis());
        }
    }
}

int main(void)
{

    /* Enable global interrupts */
    __enable_irq();
    uint32_t value = 0;
    char start_char;
    char G_char;
    char P_char;
    char G2_char;
    char G3_char;
    char A_char;
    float lumen;
    uint8_t button_status;

    cy_rslt_t result;

    /* Initialize the device and board peripherals */
    result = cybsp_init();

    /* Board init failed. Stop program execution */
    if (result != CY_RSLT_SUCCESS)
    {
        CY_ASSERT(0);
    }

    /* Initialize retarget-io to use the debug UART port */
    result = cy_retarget_io_init(ECE453_DEBUG_TX, ECE453_DEBUG_RX,
                                 CY_RETARGET_IO_BAUDRATE);
    /* retarget-io init failed. Stop program execution */
    if (result != CY_RSLT_SUCCESS)
    {
        CY_ASSERT(0);
    }

    /* Initialize the User LEDs */
    result = cyhal_gpio_init(ECE453_USR_LED, CYHAL_GPIO_DIR_OUTPUT,
                             CYHAL_GPIO_DRIVE_STRONG, CYBSP_LED_STATE_OFF);

    result = usr_btn_init();
    printf("* -- Initializing I2C Bus\n\r");
    i2c_init();

    // send_crash_ble = 1; /// remove meee

    /* GPIO init failed. Stop program execution */
    if (result != CY_RSLT_SUCCESS)
    {
        printf("Error initializing the timer\r\n");
        CY_ASSERT(0);
    }

    // TURRET INIT
    result = cyhal_gpio_init(TURRET_PIN, CYHAL_GPIO_DIR_OUTPUT, CYHAL_GPIO_DRIVE_STRONG, false);
    CY_ASSERT(CY_RSLT_SUCCESS == result);

    accelerometer_IIS328DQTR_init();
    global_timer();

    /* \x1b[2J\x1b[;H - ANSI ESC sequence for clear screen */
    printf("\x1b[2J\x1b[;H");
    printf("PSoC 6 MCU With BLE Connectivity Find Me\r\n\n");

    motor_pwm_init(&pwm_obj_drive_train);
    servo_pwm_init(&pwm_obj_servo);
    ble_findme_init();

    cyhal_gpio_init(P12_7, CYHAL_GPIO_DIR_OUTPUT, CYHAL_GPIO_DRIVE_STRONG, false);

    uart_init();
    for (;;)
    {
        turret_fire_ble();
        ble_findme_process();
        global_timer_peripherals();
        start_char = uart_get_char();
        G_char = uart_get_char();
        P_char = uart_get_char();
        G2_char = uart_get_char();
        G3_char = uart_get_char();
        A_char = uart_get_char();
        if (((int)start_char == 36) && ((int)G_char == 71) && ((int)P_char == 80) && ((int)G2_char == 71) && ((int)G3_char == 71) && ((int)A_char == 65))
        {
            if (PERIPHERAL_LOG_ON)
            {
                printf("%c%c%c%c%c%c", start_char, G_char, P_char, G2_char, G3_char, A_char);
            }
            char gps_style[6] = {start_char, G_char, P_char, G2_char, G3_char, A_char};
            char gps_style_chosen[6] = "$GPGGA";

            for (int i = 0; i < 197; i++)
            {
                char gps_data;
                gps_data = uart_get_char();
                if (PERIPHERAL_LOG_ON)
                {
                    // printf("check\r\n");
                    printf("%c", gps_data);
                }

                GPS_BUFFER[i] = gps_data;
            }
            if (strcmp(gps_style_chosen, gps_style) == 0)
            {
                // n1, e1
                char **gps_list = NULL;
                // this is the GPS style chosen
                int gps_len = gps_split(GPS_BUFFER, ',', &gps_list);
                if (gps_list[1] != NULL && isdigit(gps_list[1][0]) &&// latitude
                    gps_list[2] != NULL && isalpha(gps_list[2][0]) &&// N/s
                    gps_list[3] != NULL && isdigit(gps_list[3][0]) &&// longitude
                    gps_list[4] != NULL && isalpha(gps_list[4][0])  // E/W
                )
                {
                    for (int j = 0; j < gps_len; j++){
                        printf("%s", gps_list[j]);
                    }
                    // printf("\r\n");
                    // printf("----------%s-----------\r\n", gps_list[1]);
                    // printf("----------%s-----------\r\n", gps_list[2]);
                    // printf("----------%s-----------\r\n", gps_list[3]);
                    // printf("----------%s-----------\r\n", gps_list[4]);
                    gps_latitude = gps_list[1];
                    gps_N_1_S_0 = atoi(gps_list[2]);
                    gps_longitude = gps_list[3];
                    gps_E_1_W_0 = atoi(gps_list[4]);
                }
                free(gps_list);
            }
        }
    }
}

/* END OF FILE */

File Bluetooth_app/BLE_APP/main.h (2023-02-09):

/*
 * main.h
 *
 *  Created on: Aug 30, 2022
 *      Author: TEAM RCXD ©
 */

#ifndef MAIN_H_
#define MAIN_H_


#define ECE453_USR_BTN P5_6
#define ECE453_USR_LED P5_5


#define TURRET_PIN P5_3

#define ECE453_DEBUG_TX	P5_1
#define ECE453_DEBUG_RX P5_0

/*******************************************************************************
* Macros
*******************************************************************************/
#define PWM_FREQUENCY (100)
#define PWM_DUTY_CYCLE (50.0f)

////////////////////// Global Variable for storing BLE PWM ////////////////
extern volatile int ble_duty_cycle_drive_train;
extern volatile int ble_duty_cycle_servo;
extern cyhal_pwm_t pwm_obj_drive_train;
extern cyhal_pwm_t pwm_obj_servo;
extern volatile int send_crash_ble;
extern volatile int turret_fire;
extern volatile uint8_t GPS_BUFFER[200];


extern volatile char* gps_latitude;
extern volatile char *gps_longitude;
extern volatile int gps_N_1_S_0;
extern volatile int gps_E_1_W_0;

///////////////////////////////////////////////////////////////////////////

#include "leds.h"
#include "push_button.h"
#include "console.h"
#include "i2c.h"
#include "at42qt2120.h"

#include <stdio.h>
#include "stdlib.h"

#endif /* MAIN_H_ */

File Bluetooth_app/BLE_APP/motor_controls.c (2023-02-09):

#include "motor_controls.h"

void servo_pwm_init(cyhal_pwm_t *pwm_obj_servo){
    cy_rslt_t result;
    // Direction control
    result = cyhal_gpio_init(SERVO_IN1, CYHAL_GPIO_DIR_OUTPUT, CYHAL_GPIO_DRIVE_STRONG, false);
    CY_ASSERT(CY_RSLT_SUCCESS == result);
    result = cyhal_gpio_init(SERVO_IN2, CYHAL_GPIO_DIR_OUTPUT, CYHAL_GPIO_DRIVE_STRONG, false);
    CY_ASSERT(CY_RSLT_SUCCESS == result);
    
    // speed control
    result = cyhal_pwm_init(pwm_obj_servo, PWM_servo, NULL);
    CY_ASSERT(CY_RSLT_SUCCESS == result);
    /* Start the PWM output */
    result = cyhal_pwm_start(pwm_obj_servo);
    CY_ASSERT(CY_RSLT_SUCCESS == result);

    return;
}

void servo_pwm_set(cyhal_pwm_t *pwm_obj_servo, int pwm_frequency, float pwm_duty_cycle, bool servo_on, bool right){
    cy_rslt_t result;
    bool write_val = false; //write_val used for IN1 and IN2 for direction output of Hbridge
    
    if (!servo_on){  // SERVO OFF
        cyhal_gpio_write(SERVO_IN1, write_val);
        cyhal_gpio_write(SERVO_IN2, write_val);
        return;
    }
    else //forward or backward state
    {
        cyhal_gpio_write(SERVO_IN1, right);
        cyhal_gpio_write(SERVO_IN2, !right); 
    }
    
    result = cyhal_pwm_set_duty_cycle(pwm_obj_servo, pwm_duty_cycle, pwm_frequency);
    CY_ASSERT(CY_RSLT_SUCCESS == result);


    return;
}

void motor_pwm_init(cyhal_pwm_t *pwm_obj_drive_train){
    cy_rslt_t result;
    // Direction control
    result = cyhal_gpio_init(DRIVE_TRAIN_IN1, CYHAL_GPIO_DIR_OUTPUT, CYHAL_GPIO_DRIVE_STRONG, false);
    CY_ASSERT(CY_RSLT_SUCCESS == result);
    result = cyhal_gpio_init(DRIVE_TRAIN_IN2, CYHAL_GPIO_DIR_OUTPUT, CYHAL_GPIO_DRIVE_STRONG, false);
    CY_ASSERT(CY_RSLT_SUCCESS == result);
    
    // speed control
    result = cyhal_pwm_init(pwm_obj_drive_train, PWM_drive_train, NULL);
    CY_ASSERT(CY_RSLT_SUCCESS == result);
    /* Start the PWM output */
    result = cyhal_pwm_start(pwm_obj_drive_train);
    CY_ASSERT(CY_RSLT_SUCCESS == result);

    return;
}

void motor_pwm_set(cyhal_pwm_t *pwm_obj_drive_train, int pwm_frequency, float pwm_duty_cycle, bool motor_1_on, bool motor_2_on, bool forward){
    cy_rslt_t result;
    bool write_val = false; //write_val used for IN1 and IN2 for direction output of Hbridge
    
    if (motor_1_on == false && motor_2_on == false){  // MOTORS OFF
        cyhal_gpio_write(DRIVE_TRAIN_IN1, write_val);
        cyhal_gpio_write(DRIVE_TRAIN_IN2, write_val);
        return;
    }
    else //forward or backward state
    {
        cyhal_gpio_write(DRIVE_TRAIN_IN1, forward);
        cyhal_gpio_write(DRIVE_TRAIN_IN2, !forward); 
    }
    
    result = cyhal_pwm_set_duty_cycle(pwm_obj_drive_train, pwm_duty_cycle, pwm_frequency);
    CY_ASSERT(CY_RSLT_SUCCESS == result);


    return;
}

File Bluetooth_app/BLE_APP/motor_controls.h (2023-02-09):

/*
 * motor_controls.h
 *
 *  Created on: Nov 6, 2022
 *      Author: sreen
 */

#ifndef MOTOR_CONTROLS_H_
#define MOTOR_CONTROLS_H_

/***** DRIVE TRAIN ******/ /// both motor
#define PWM_drive_train P10_4 //pwm pwm function parameter 1 red
#define DRIVE_TRAIN_IN1 P10_5//out 1 gpio orange
#define DRIVE_TRAIN_IN2 P9_5 //out 2 gpio yellow


/***** SERVO ******/
#define PWM_servo P10_6 //blue
#define SERVO_IN1 P10_3 //purple
#define SERVO_IN2 P12_6 //green


// //front motor
// #define PWM_drive_train2 P9_4//pwm pwm function parameter 2 red
// #define DRIVE_TRAIN_IN3 P10_4 //out 3 gpio yellow
// #define DRIVE_TRAIN_IN4 P10_6//out 4 gpio orange


#include "cy_pdl.h"
#include "cy_retarget_io.h"
#include "cybsp.h"
#include "cyhal.h"
#include "ble_findme.h"
#include "main.h"
#include "usr_btn.h"

/***** DRIVE TRAIN ******/
void motor_pwm_set(cyhal_pwm_t *pwm_obj_drive_train, int pwm_frequency, float pwm_duty_cycle, bool motor_1_on, bool motor_2_on, bool forward);
void motor_pwm_init(cyhal_pwm_t *pwm_obj_drive_train);
/***** SERVO ******/
void servo_pwm_init(cyhal_pwm_t *pwm_obj_servo);
void servo_pwm_set(cyhal_pwm_t *pwm_obj_servo, int pwm_frequency, float pwm_duty_cycle, bool servo_on, bool right);

#endif /* MOTOR_CONTROLS_H_ */
